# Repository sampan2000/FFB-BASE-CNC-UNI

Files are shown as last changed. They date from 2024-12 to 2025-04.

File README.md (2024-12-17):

# FFB-BASE-CNC-UNI
通用FFB底座CNC版本<br>
为适配灵足03和伺泰威GIM8108-8电机而改进的底座，只需要更换中间连杆就可以适配两种电机。今后改进都以这个图纸为基础。灵足03的额定扭矩有20nm，如果不加延长杆，其实力矩有点过剩了。伺泰威8108性价比很高，额定8nm的扭矩，可以满足绝大多数游戏向玩家。<br>
零件根据铨洲CNC打样的要求，对工艺和尺寸进行了优化，尽量降低成本。在加工所有侧孔和所有螺纹孔攻丝的情况下，打样灵足03用的一套价格大概260块，如果去掉侧孔、不攻丝，打样成本可以降到大概110块。<br>
安装步骤为：<br>
1.先装好底板和roll电机座
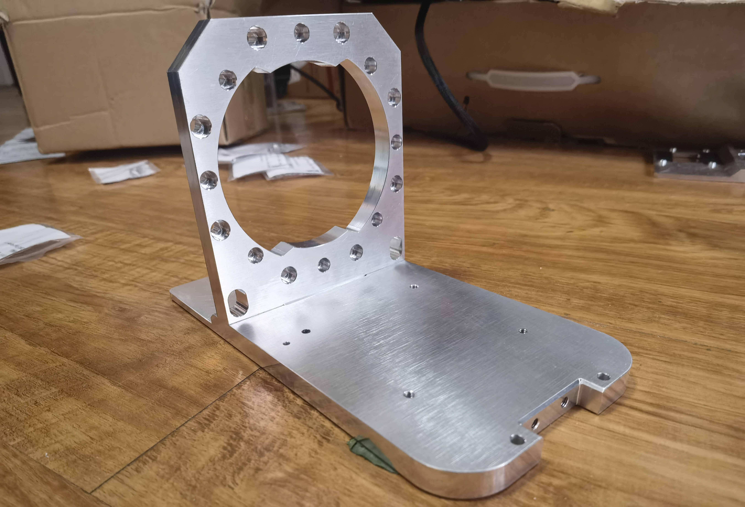
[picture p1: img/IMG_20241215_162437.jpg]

2.组装连杆
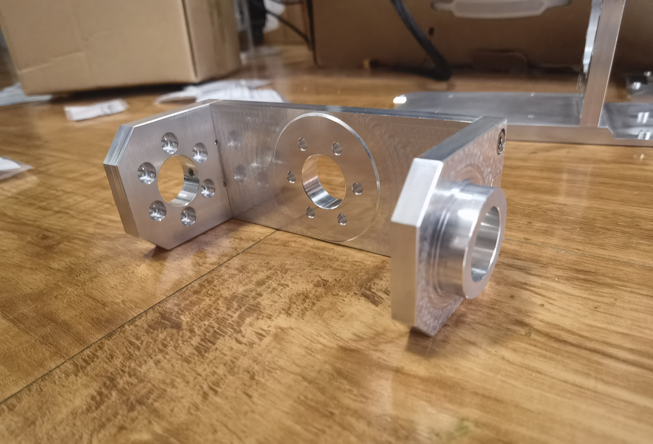
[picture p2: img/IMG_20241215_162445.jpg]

3.把轴承装进轴承座，这里配合比较紧，我用台钳压的
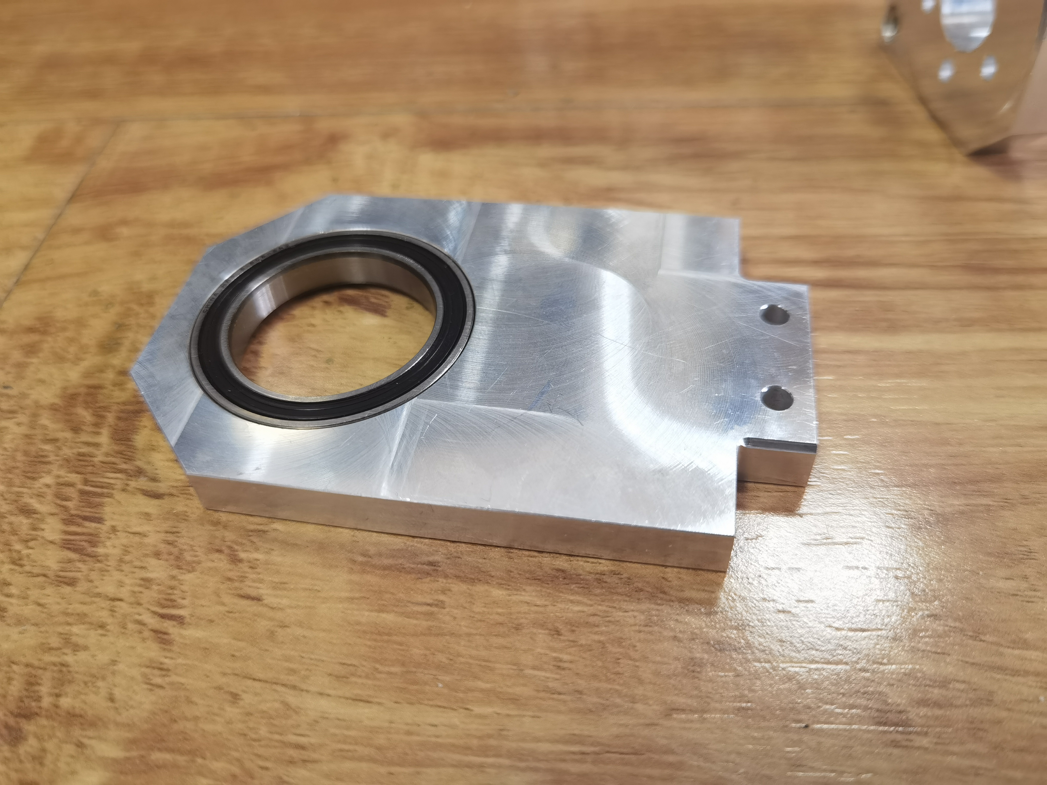
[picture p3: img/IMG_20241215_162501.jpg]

4.装上roll电机
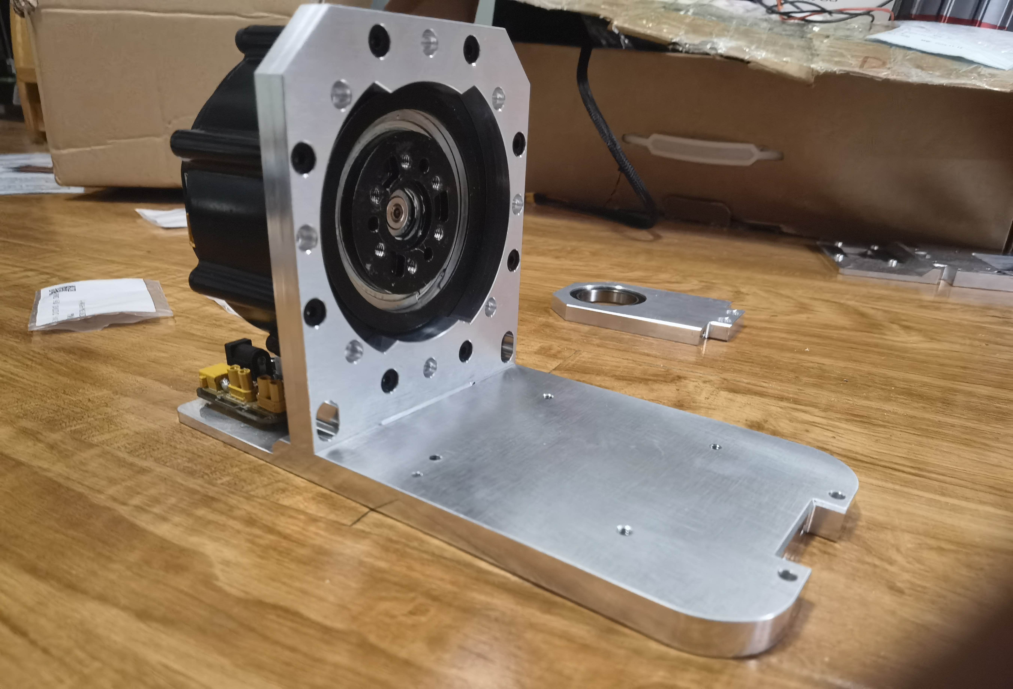
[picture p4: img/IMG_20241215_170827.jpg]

5.把连杆固定到roll电机上
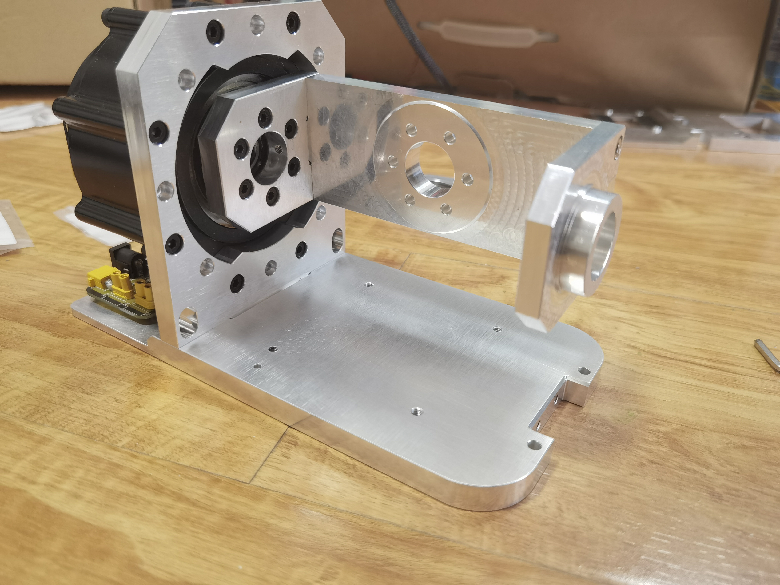
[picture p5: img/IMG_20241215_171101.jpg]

6.安装轴承座
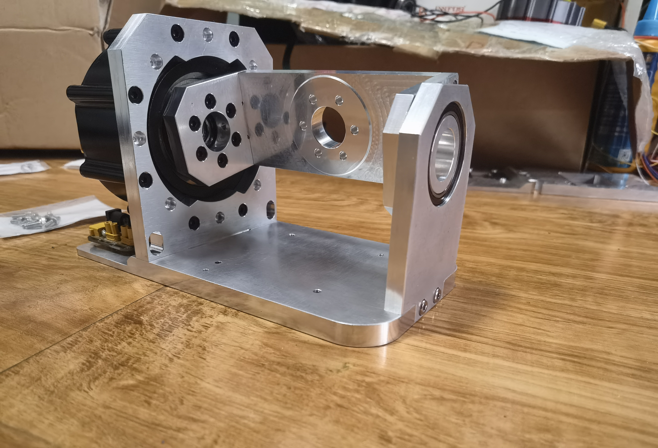
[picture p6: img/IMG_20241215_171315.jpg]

7.安装pitch电机
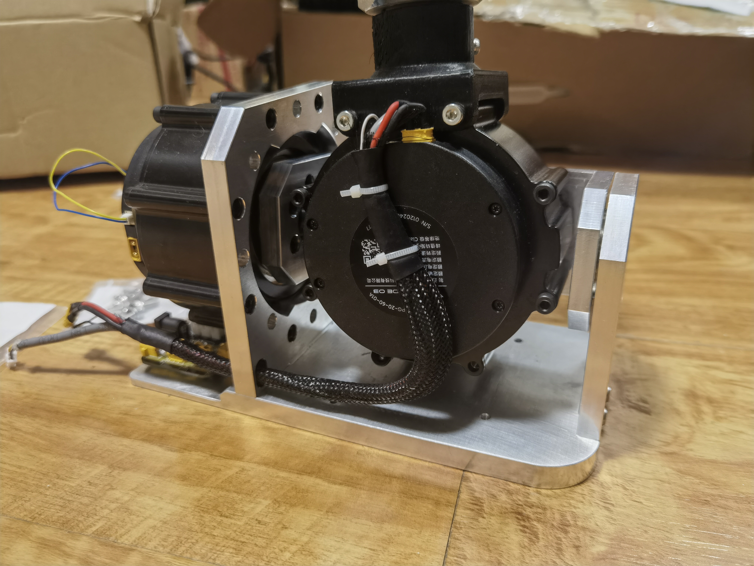
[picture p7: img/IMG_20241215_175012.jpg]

除了6个结构件使用CNC以外，杆头底座目前CNC成本太高，仍然采用3D打印。
<br>BOM
<table>
<tr><th rowspan='2'>名称</th><th>灵足03</th><th>GIM8108</th></tr>
<tr><th>数量</th><th>数量</th></tr>
<tr><td>M4x12杯头螺钉</td><td>35</td><td>15</td></tr>
<tr><td>M3x10杯头螺钉</td><td>2</td><td>22</td></tr>
<tr><td>6806轴承</td><td colspan='2' align='center'>1</td></tr>
</table>
<br>
补充：
<br>1.“通用FFB底座CNC版本.step”这个文件是全图，里面包含了灵足和8108电机需要的全部部件，自己得根据自己用的电机选择，不用全部打样
<br>2.为了方便，我把打样的独立文件放在“CNC打样用的分立部件图”目录里面，其中“通用”里面的3个件都要用到，另外两个目录里面的根据电机选择
<br>3.总图里面的底板和电机座上在两侧加了4个孔，是打算将来安装外壳用的，我打样的时候把这侧孔去掉了，如果要一起加工出来，会贵差不多70块
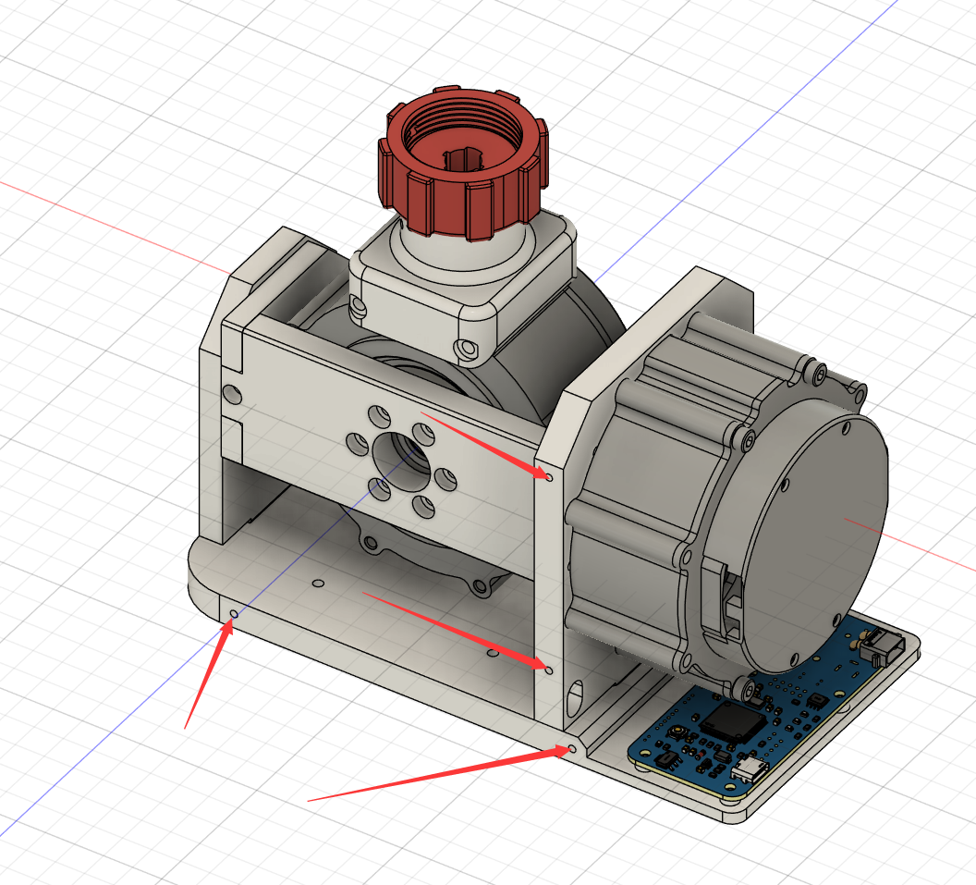
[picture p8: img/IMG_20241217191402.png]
<br>

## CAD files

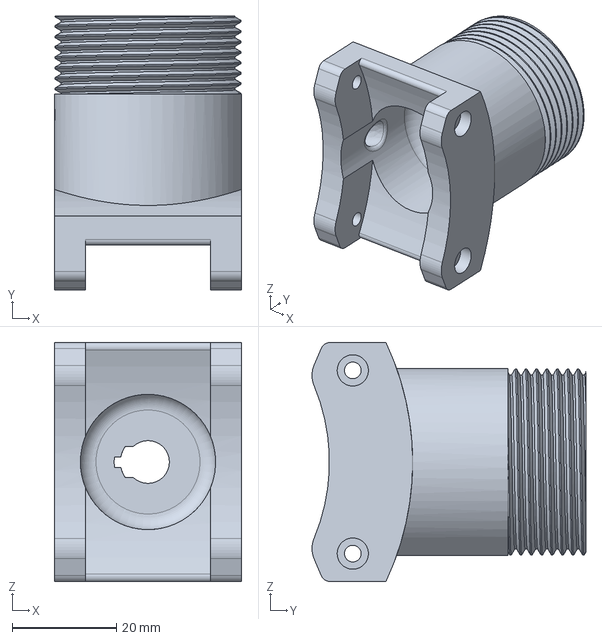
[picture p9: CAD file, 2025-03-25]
3D打印部件/8108图马杆头连接座.step
36.0 x 52.7 x 46.0 mm

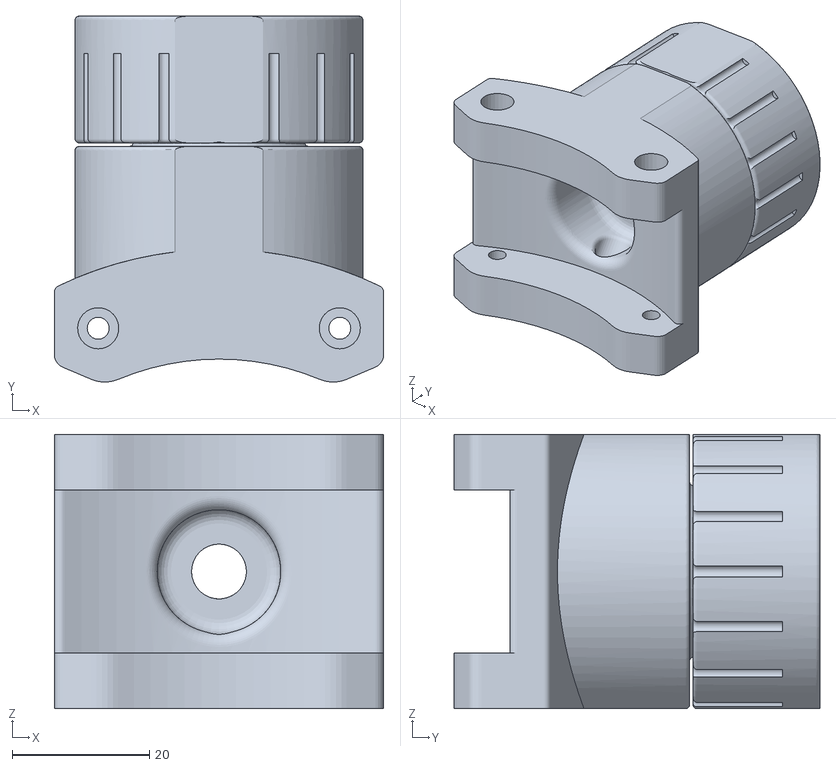
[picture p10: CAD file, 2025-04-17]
3D打印部件/stl/8108一体化ww杆头固定座.stl
48.0 x 53.3 x 40.0

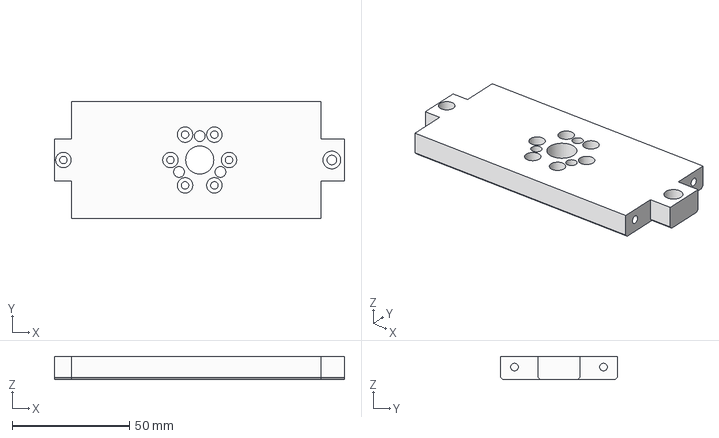
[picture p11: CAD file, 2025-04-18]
CNC打样用的分立部件图/8108电机专用/8108Pitch Motor Mount.step
123.8 x 50.0 x 10.0 mm

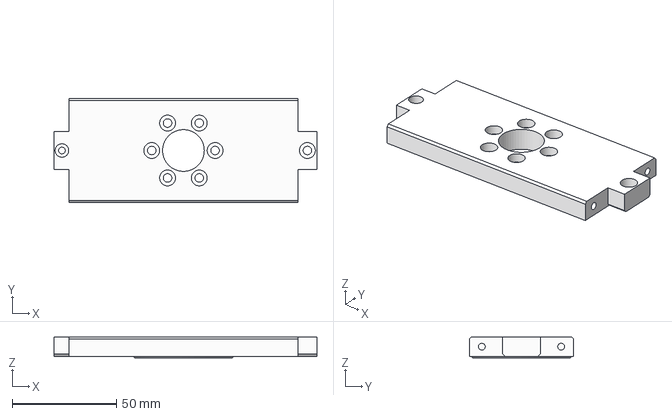
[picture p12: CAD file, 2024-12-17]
CNC打样用的分立部件图/灵足03专用/灵足03Pitch Motor Mount.step
126.0 x 50.0 x 10.0 mm

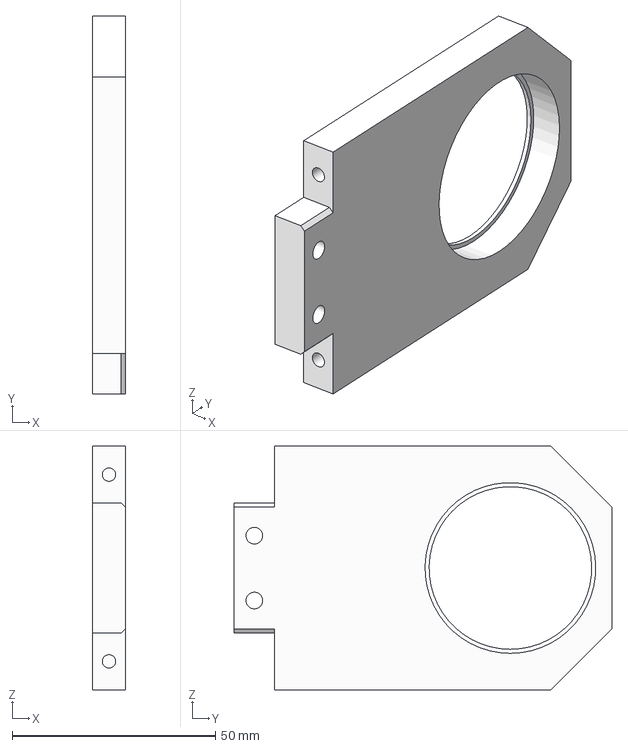
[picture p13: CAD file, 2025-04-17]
CNC打样用的分立部件图/通用/轴承支座.step
8.00 x 93.0 x 60.0 mm

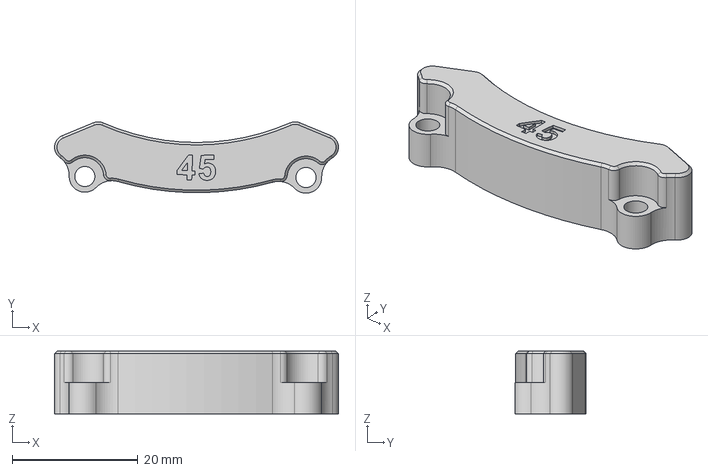
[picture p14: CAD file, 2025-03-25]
3D打印部件/8108俯仰电机下部限位块45.step
45.2 x 11.4 x 10.0 mm

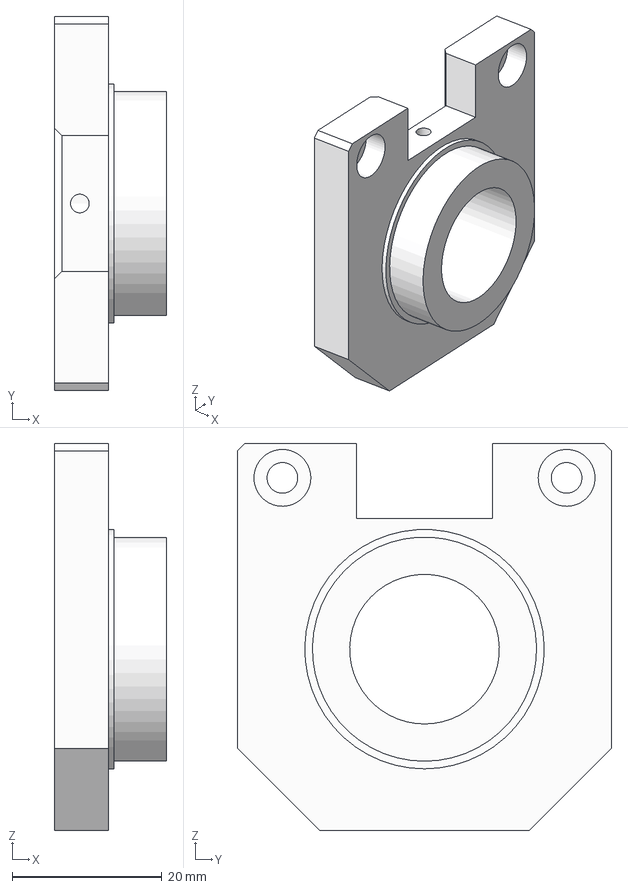
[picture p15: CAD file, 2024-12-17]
CNC打样用的分立部件图/8108电机专用/8108Pitch Bearing Linkage.step
15.0 x 50.0 x 51.8 mm

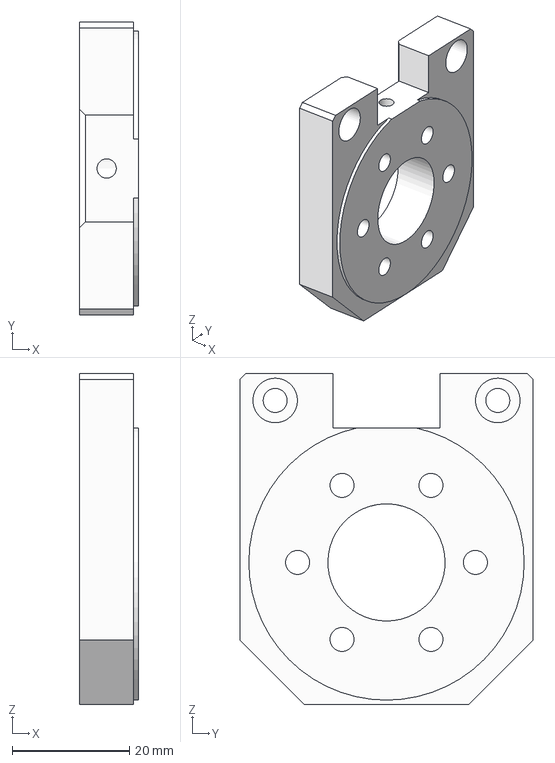
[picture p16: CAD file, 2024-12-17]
CNC打样用的分立部件图/灵足03专用/灵足03Pitch Motor Linkage.step
10.0 x 50.0 x 56.5 mm

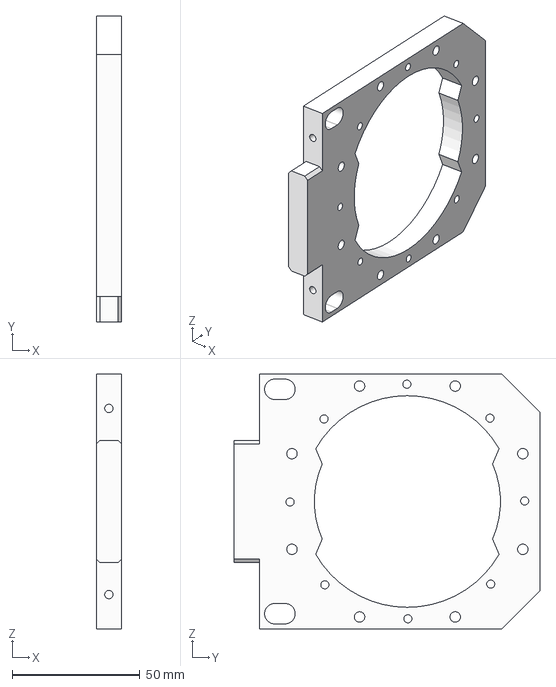
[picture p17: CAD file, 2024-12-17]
CNC打样用的分立部件图/通用/Roll Motor Mount.step
10.0 x 120.0 x 100.0 mm

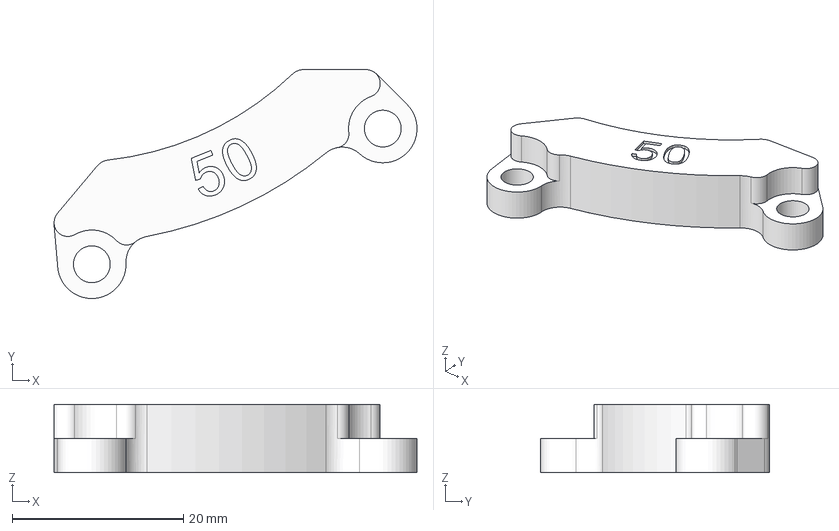
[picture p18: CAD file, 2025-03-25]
3D打印部件/灵足03俯仰电机下部限位50.step
42.4 x 26.8 x 8.00 mm

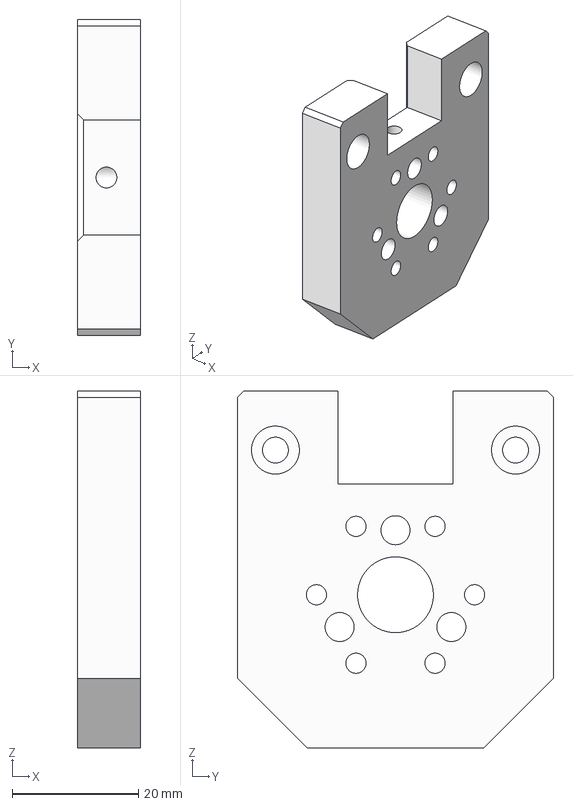
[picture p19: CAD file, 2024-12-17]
CNC打样用的分立部件图/8108电机专用/8108Pitch Motor Linkage.step
10.0 x 50.0 x 56.5 mm

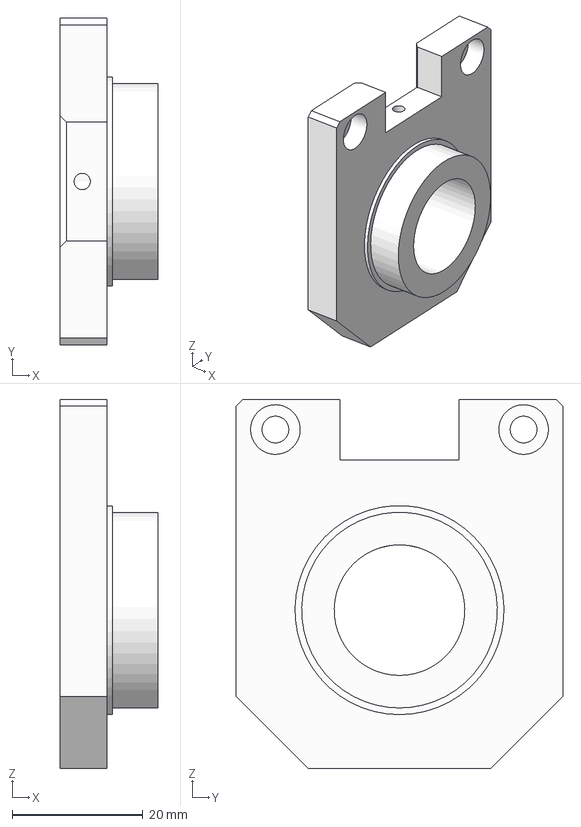
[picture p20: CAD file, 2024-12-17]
CNC打样用的分立部件图/灵足03专用/灵足03Pitch Bearing Linkage.step
15.0 x 50.0 x 56.5 mm

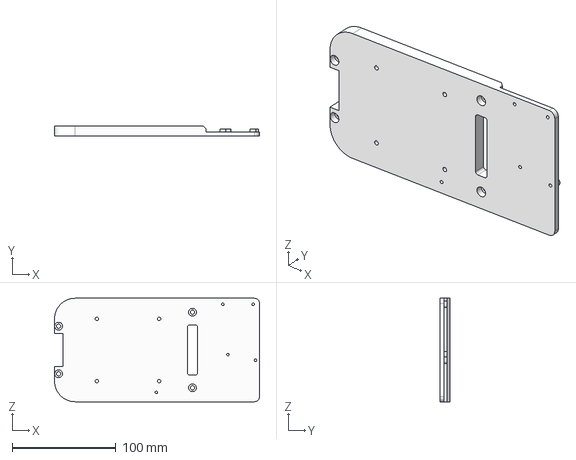
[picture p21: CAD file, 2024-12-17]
CNC打样用的分立部件图/通用/底板 v2.step
198.0 x 10.0 x 100.0 mm

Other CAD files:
3D打印部件/灵足03图马杆头连接座.step
3D打印部件/stl/8108俯仰电机下部限位块45.stl
3D打印部件/stl/8108图马杆头连接座.stl
3D打印部件/stl/灵足03俯仰电机下部限位50.stl
3D打印部件/stl/灵足03图马杆头连接座.stl

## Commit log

2024-12-15 完善说明
2024-12-15 修改说明
2024-12-16 Update 通用FFB底座CNC版本.step
    修正打样发现的8108组件问题
2024-12-16 Update README.md
    更新了BOM
2024-12-17 增加分立部件图
    增加了CNC打样需要的分立部件图，更新了说明
    [8108Pitch Bearing Linkage.step, 8108Pitch Motor Linkage.step, 8108Pitch Motor Mount.step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]
2025-03-25 增加了几个打印件
    增加了俯仰电机下部限位块和安装图马杆头的3D打印件
    [8108俯仰电机下部限位块45.step, 8108俯仰电机下部限位块45.stl, 8108图马杆头连接座.step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]
2025-03-25 修正了一下8108图马杆头座
    [8108图马杆头连接座.step, 8108图马杆头连接座.stl]
2025-03-25 更新了总图
2025-04-17 优化更新
    1、增加了适配8108电机的ww杆头一体化打印的固定座
    2、修改8108的部分图纸，避免在铨州打样时出现漏切
    [8108Pitch Motor Mount.step, 8108一体化ww杆头固定座.stl, 轴承支座.step]
2025-04-18 更新8108会漏切的零件图
    上次更新的文件有错，重新上传
    [8108Pitch Motor Mount.step]
